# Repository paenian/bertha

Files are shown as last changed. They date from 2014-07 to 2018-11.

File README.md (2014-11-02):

bertha
======

Large format Rostock style printer, built with aluminum extrusions.

My plan is to design a large printer, emphasizing quality over cost.  Ideally there will be the 'full' version, and then various lower cost options.

The design of the plastic parts contained here is complete - that's not to say they won't be updated, just that everything in here is functional.

I am working on build instructions in a blog over here: http://berthareprap.blogspot.com/2013/05/mark-4-finally.html
I am currently constructing the very first machine, so instructions are coming out as I get build time.

Bill of Materials
===============
Frame BOM
-----
m3 x 8mm...........12&nbsp;&nbsp;&nbsp;&nbsp;Motor mounting<br>
m3 x 10mm..........12&nbsp;&nbsp;&nbsp;&nbsp;Bearing bar side mounts<br>
m3 x 16mm..........12&nbsp;&nbsp;&nbsp;&nbsp;Rod End clamps - use to hold rods in place temporarily, while glue sets up.<br>
m3 x 22mm..........12&nbsp;&nbsp;&nbsp;&nbsp;Rod End attachments - clamp the rod ends onto the bearing bar<br>
m3 x nuts..........24&nbsp;&nbsp;&nbsp;&nbsp;12 for the rod end clamp, 12 for bearing bar attachment<br>
m3 x locknut.......12&nbsp;&nbsp;&nbsp;&nbsp;rod end attachments<br>
<br>
m5 x 30mm..........15&nbsp;&nbsp;&nbsp;&nbsp;12 for V wheel mounts, 3 for idler mounts<br>
m5 x 10mm low p....72&nbsp;&nbsp;&nbsp;&nbsp;12 for each bracket<br>
m5 x nut...........12&nbsp;&nbsp;&nbsp;&nbsp;6 idler, 6 belt mount<br>
m5 x washer........6&nbsp;&nbsp;&nbsp;&nbsp;v-wheel clamping<br>
m5 x T-nut.........72&nbsp;&nbsp;&nbsp;&nbsp;12 for each bracket<br>
<br>
623 bearings.......36&nbsp;&nbsp;&nbsp;&nbsp;6 for each bearing bar.<br>
m3 x 2mm spacer....12&nbsp;&nbsp;&nbsp;&nbsp;http://www.mcmaster.com/#94669a210/=tgrbjv  4.5mm outside diameter.  6mm OD might be better, but they're significantly more expensive.<br>
8mm square carbon fiber rods....6&nbsp;&nbsp;&nbsp;&nbsp;Length forthcoming.  Gotta measure 'em.<br>
<br>
OpenBuilds Part Store bits
-----
1m v-rails.........3&nbsp;&nbsp;&nbsp;&nbsp;http://openbuildspartstore.com/black-v-slot-20-x-60mm/<br>
mini-V  wheel kit..12&nbsp;&nbsp;&nbsp;&nbsp;http://openbuildspartstore.com/mini-v-wheel-kit/<br>
idler kit..........3&nbsp;&nbsp;&nbsp;&nbsp;http://openbuildspartstore.com/smooth-idler-pulley-kit/<br>
Eccentric Spacers..6&nbsp;&nbsp;&nbsp;&nbsp;http://openbuildspartstore.com/eccentric-spacers/<br>
<br>
Misumi
-----
350mm 2060 extrusion, HFS5-2060-350.  This can be larger if you like, but you'll need to recalculate the triangles and rod lengths.<br>
<br>
Printed Bits
-----
Idler Bracket......6<br>
Idler Slider.......6<br>
Motor Bracket......6<br>
Hotend Effector....1&nbsp;&nbsp;&nbsp;&nbsp;These are in the new effectors directory!<br>
Rail Effector......3&nbsp;&nbsp;&nbsp;&nbsp;These are in the new effectors directory!<br>
Bearing Bar........6&nbsp;&nbsp;&nbsp;&nbsp;These are in the new effectors directory!<br>
Rod End...........12&nbsp;&nbsp;&nbsp;&nbsp;These are in the new effectors directory!<br>
<br>
<br>
<br>
<br>
Paul Chase.

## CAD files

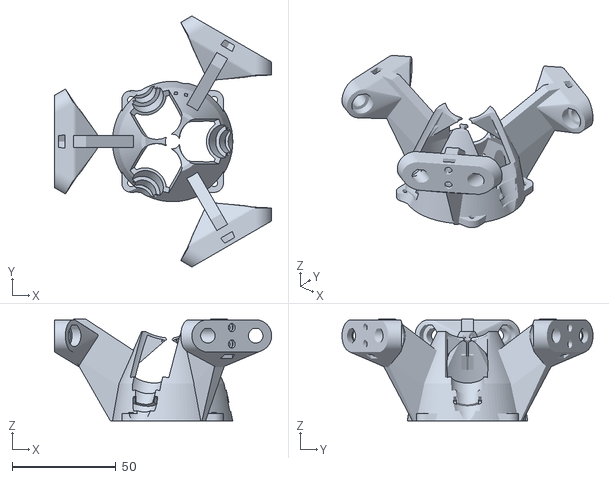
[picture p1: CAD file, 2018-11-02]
new_effectors/diamond_hotend_assembly_fixed.obj
104.7 x 120.9 x 49.0

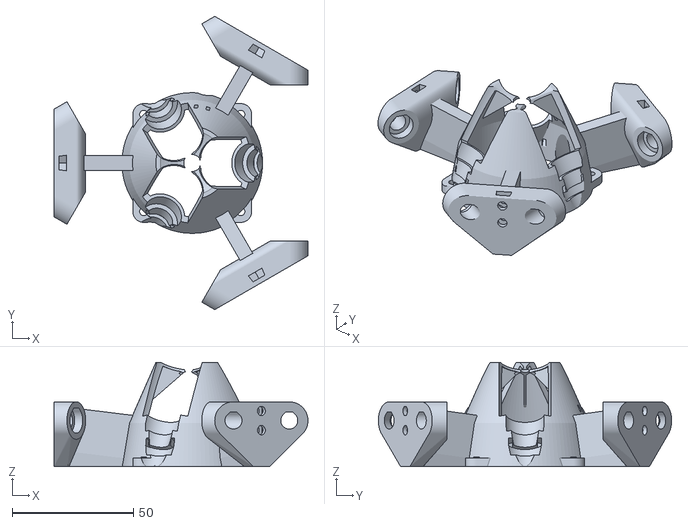
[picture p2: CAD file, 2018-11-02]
new_effectors/diamond_hotend_assembly.stl
104.7 x 120.9 x 43.0

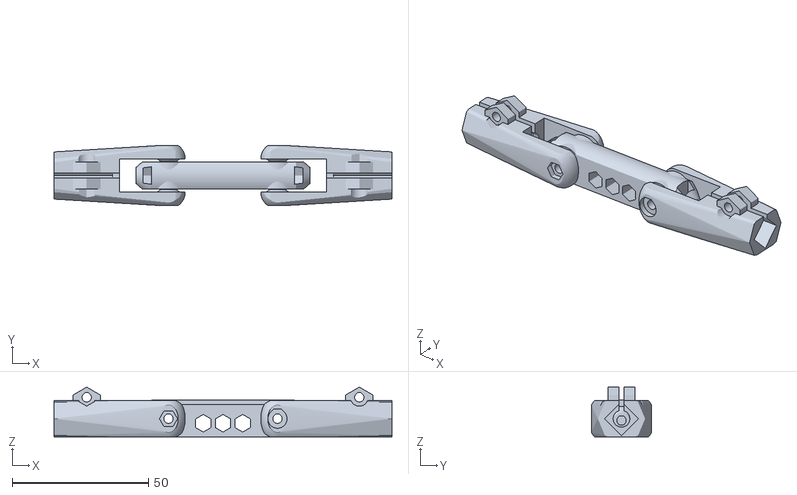
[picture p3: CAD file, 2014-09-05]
new_effectors/bearing_bar_assembly.stl
124.0 x 22.0 x 18.3

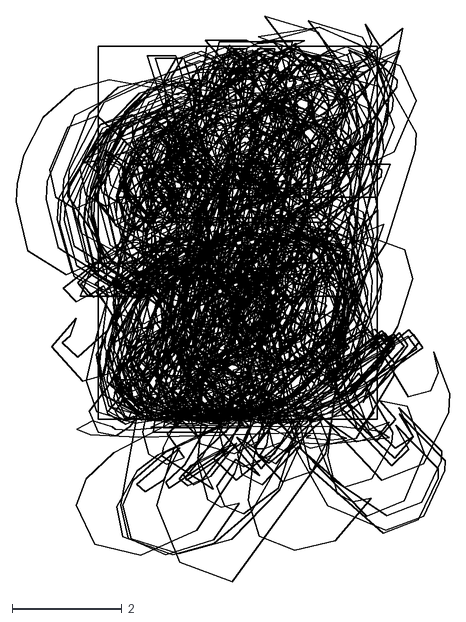
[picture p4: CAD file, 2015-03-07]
doors/Writescad/BlackRose.dxf
7.90 x 10.3

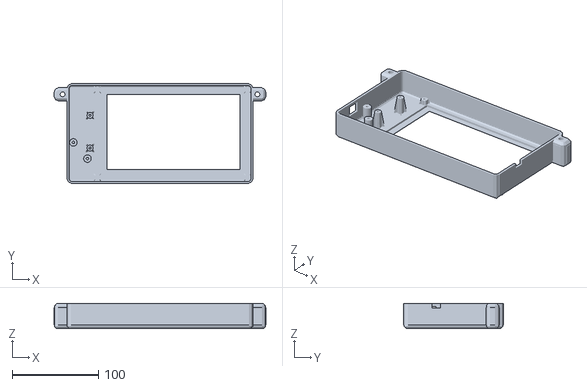
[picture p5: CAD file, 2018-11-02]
duet/PanelDueEnclosure.stl
246.4 x 115.8 x 29.1

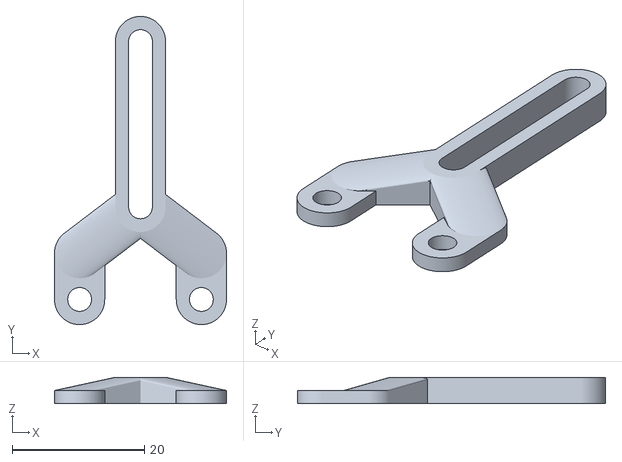
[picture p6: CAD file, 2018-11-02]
new_effectors/ir_sensor_mount.stl
26.0 x 46.6 x 4.00

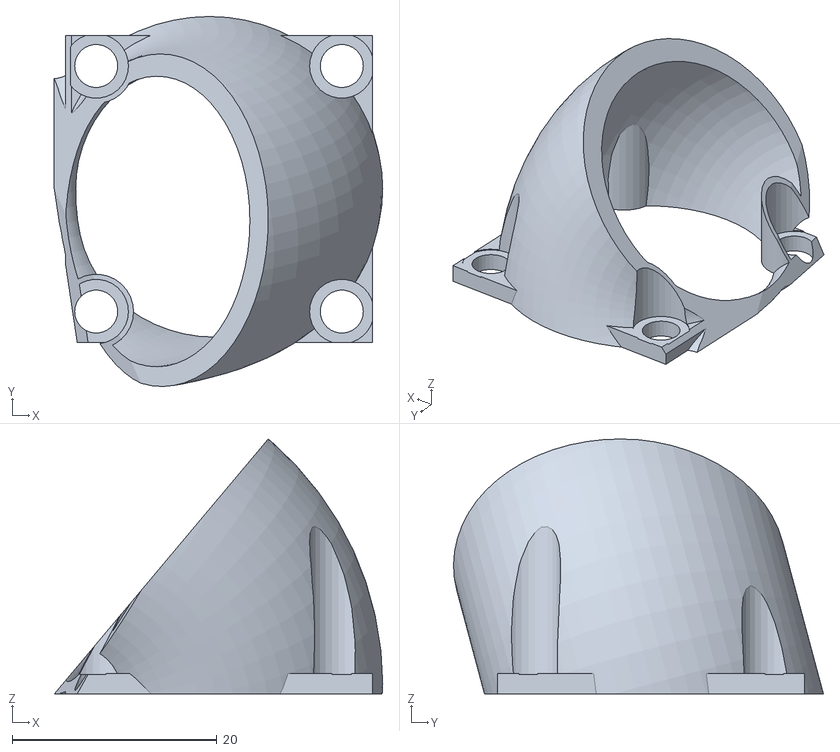
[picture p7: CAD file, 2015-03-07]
tinyduct.stl
32.1 x 36.2 x 24.9

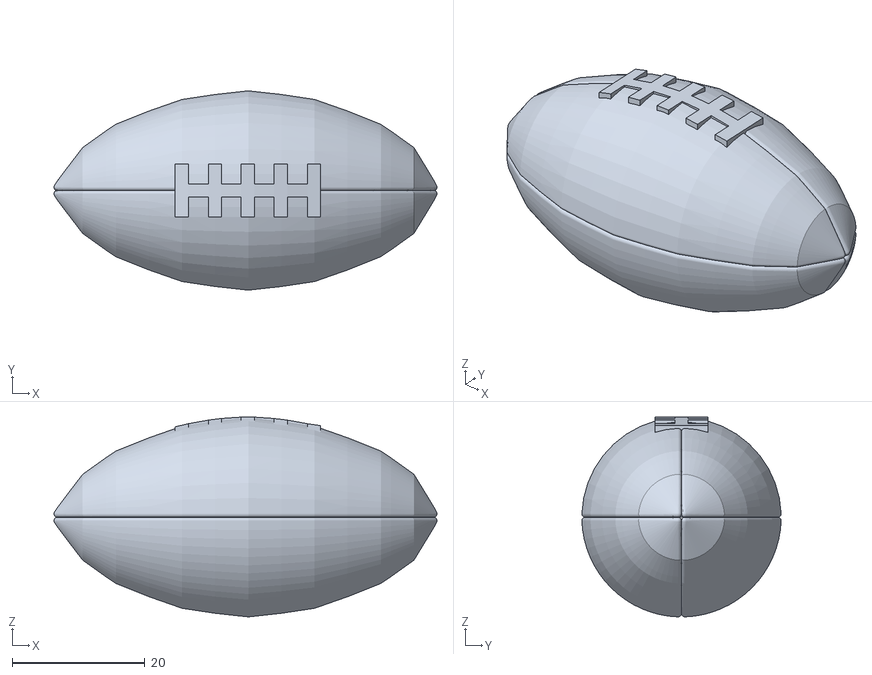
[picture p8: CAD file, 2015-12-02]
trophy/football.stl
57.8 x 30.1 x 30.2

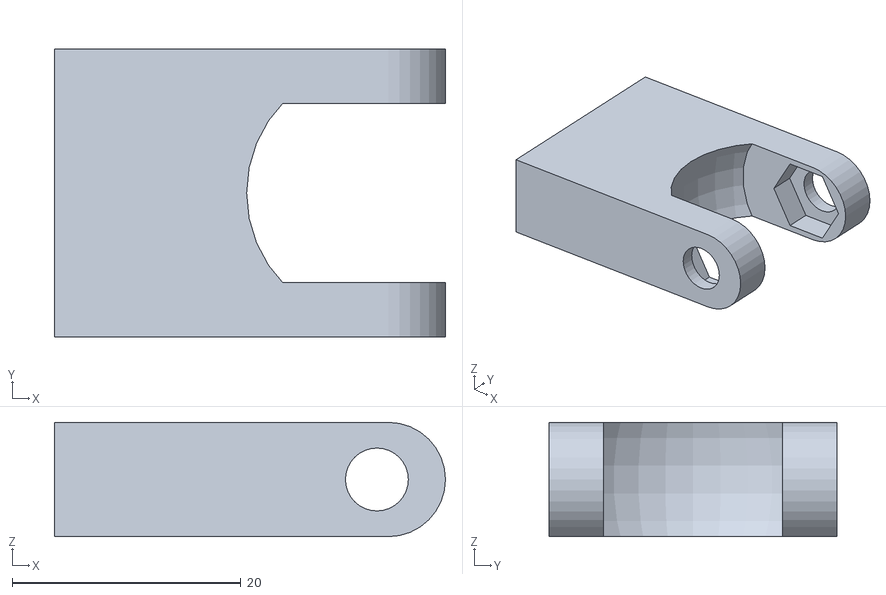
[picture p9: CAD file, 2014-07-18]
ujoints/rodend_inset.stl
34.2 x 25.2 x 10.0

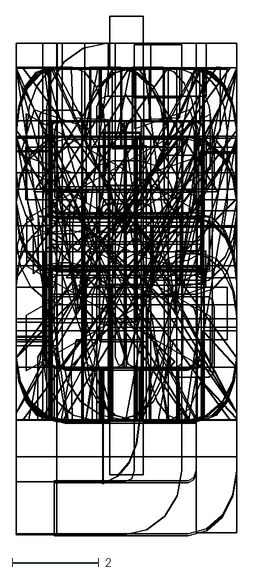
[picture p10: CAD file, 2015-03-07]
doors/Writescad/orbitron.dxf
5.08 x 12.0

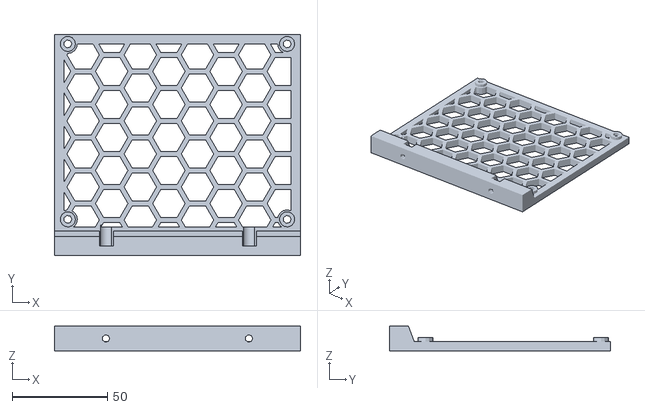
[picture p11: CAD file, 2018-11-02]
duet/duet_base.stl
129.0 x 116.0 x 13.0

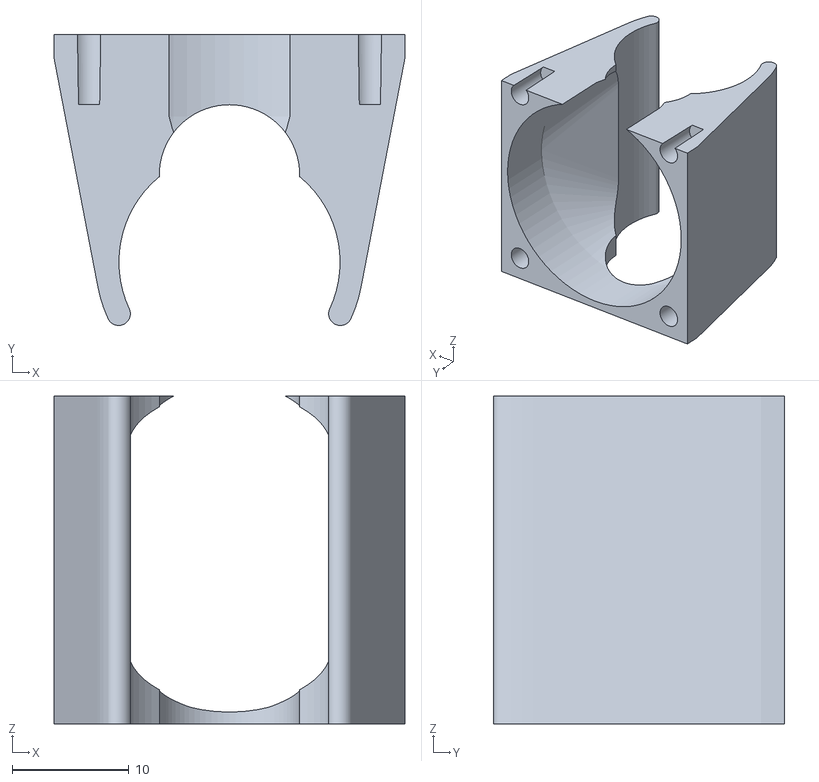
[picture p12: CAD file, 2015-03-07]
hexagon_fanshroud.stl
30.0 x 24.9 x 28.0

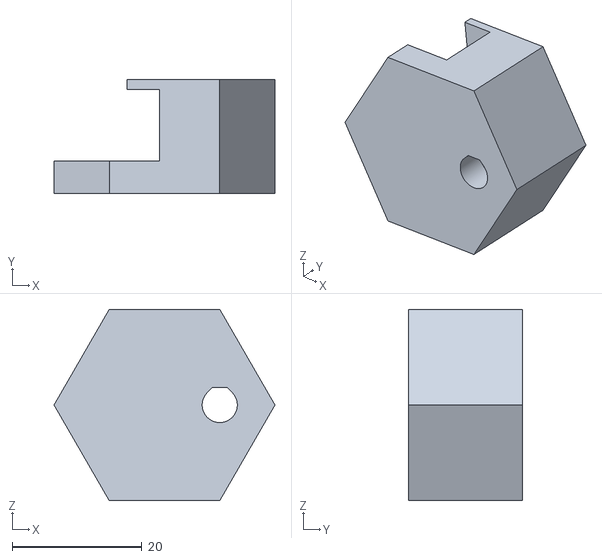
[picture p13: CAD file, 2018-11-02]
new_effectors/bed_clip.stl
34.0 x 17.5 x 29.4

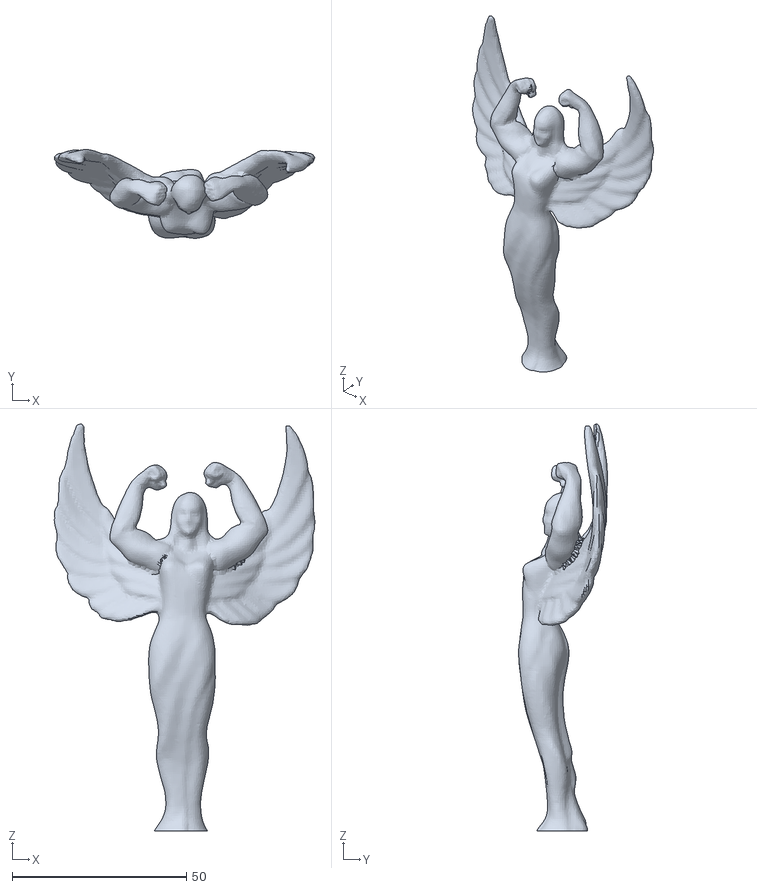
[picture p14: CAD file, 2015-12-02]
trophy/beefy_trophy.stl
74.8 x 25.5 x 116.9

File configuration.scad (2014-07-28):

$fn = 18;

slop = .2;

wall = 5;

bolt_slop = .5;
nut_slop = .85;
bolt_dia = 5+bolt_slop;
bolt_rad = bolt_dia/2;
bolt_cap_dia = 10+bolt_slop;
bolt_cap_rad = bolt_cap_dia/2;
nut_dia = 9+nut_slop;
nut_rad = nut_dia/2;
nut_height = 3.25;
lock_nut_height = 5.25;

m3bolt_dia = 3+bolt_slop;
m3bolt_rad = m3bolt_dia/2;
m3nut_dia = 6.1+nut_slop;
m3nut_rad = m3nut_dia/2;
m3nut_height = 3;

ext_x = 20+slop;
ext_y = 60+slop;

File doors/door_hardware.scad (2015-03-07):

use <write.scad>

base_rad = 30;
base_h = 20;
font_size = 10;

writecylinder("K N O X",[0,0,0],base_rad,base_h/2,h=font_size);

wall=5;

h1 = "BERTHA";

for(i=[0:len(h1)]) translate([0,0,i*font_size]) rotate([90,0,0]) scale([1.5,1,1]) write(h1[len(h1)-i],t=wall*3,h=font_size,center=true, font = "Writescad/orbitron.dxf");

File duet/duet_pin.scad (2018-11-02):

$fn = 36; 

module base() {

hull() {

 cylinder(h=3, d1=6, d2=8, center=false);
 
 
 
translate([0,0,40])
 
cylinder(h=3, d1=8, d2=6, center=false);
    
translate([3,-3,3])
 
cube ([1,6,43-3-3]);  
  
translate([3,-2,1])
  
cube ([1,4,41]);      
    
}

}


module holes() {

translate([-10,-5,3+8/2])
cube ([10,10,43-3-3-8]);   

cylinder(h=43, d=4, center=false);


translate([0,0,4.5])
cylinder(h = 43-3-3-8+5, d = 6.5, center = false, $fn = 6 );


}

difference (){
base();

holes();
    
}

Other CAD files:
ujoints/core.stl
doors/Writescad/knewave.dxf
e3dv6.stl
ujoints/bearing_arms.stl
new_effectors/configuration.scad
anglefan.scad
bearing_arms.scad
bed_clip.stl
bed_mount.scad
bed_mount.stl
brackets.scad
doors/Writescad/Letters.dxf
doors/Writescad/braille.dxf
doors/write.scad
duet/PanelDueEnclosure.scad
duet/duet_base.scad
e3dv6.scad
e3dv6_fan_mount.stl
effectors.scad
fan.stl
fan_mount.stl
foot.scad
foot.stl
foot_cabletie.stl
hotend_clamp.stl
hotend_effector.stl
hotend_fan_mount.stl
hotendeffector.scad
hotendeffector_fixed.stl
idler_bracket.stl
idler_guide.scad
idler_guide.stl
idler_slider.stl
joint.scad
joint_2.scad
lcd_mount.scad
lcd_mount.stl
lm8uu_clamp.scad
motor_bracket.stl
motor_fan.stl
new_effectors/bearing_bar.stl
new_effectors/bed_mounts.scad
new_effectors/bed_mounts.stl
new_effectors/diamond_hotend_assembly.scad
new_effectors/diamond_hotend_effector.stl
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

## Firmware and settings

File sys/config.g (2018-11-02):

; Think3DPrint3D configuration file for Mini Kossel for testing Duet WiFi

; Communication and general
M111 S0                             	; Debug off
M550 PMiniKosselWiFiTest		; Machine name and Netbios name (can be anything you like)
M551 Preprap                        	; Machine password (used for FTP)
;*** If you have more than one Duet on your network, they must all have different MAC addresses, so change the last digits
M540 P0xBE:0xEF:0xDE:0xAD:0xFE:0xED 	; MAC Address
;*** Wifi Networking
; M552 S1				; Enable WiFi. Disabled for setup and testing. Enable once set up on your network.

M555 P2                           	; Set output to look like Marlin
M575 P1 B57600 S1			; Comms parameters for PanelDue

G21                                 	; Work in millimetres
G90                                	; Send absolute coordinates...
M83                                 	; ...but relative extruder moves

; Axis and motor configuration
M569 P0 S1				; Drive 0 goes forwards
M569 P1 S1				; Drive 1 goes forwards
M569 P2 S1				; Drive 2 goes forwards
M569 P3 S1				; Drive 3 goes forwards
M569 P4 S1				; Drive 4 goes forwards
M574 X2 Y2 Z2 S1			; set endstop configuration (all endstops at high end, active high)
;*** The homed height is deliberately set too high in the following - you will adjust it during calibration
M665 R105.6 L215.0 B85 H250		; set delta radius, diagonal rod length, printable radius and homed height
M666 X0 Y0 Z0				; put your endstop adjustments here, or let auto calibration find them
M350 X16 Y16 E16 I1    			; Set 16x microstepping with interpolation
M92 X80 Y80 Z80				; Set axis steps/mm
M906 X1000 Y1000 Z1000 E800 I60		; Set motor currents (mA) and increase idle current to 60%
M201 X1000 Y1000 Z1000 E1000		; Accelerations (mm/s^2)
M203 X20000 Y20000 Z20000 E3600		; Maximum speeds (mm/min)
M566 X1200 Y1200 Z1200 E1200		; Maximum instant speed changes mm/minute

; Thermistors
M305 P0 T100000 B3950 R4700 H30 L0	; Put your own H and/or L values here to set the bed thermistor ADC correction
M305 P1 T100000 B3974 R4700 H30 L0	; Put your own H and/or L values here to set the first nozzle thermistor ADC correction
M305 P2 T100000 B3974 R4700 H30 L0	; Put your own H and/or L values here to set the second nozzle thermistor ADC correction
M570 S180				; Hot end may be a little slow to heat up so allow it 180 seconds

; Fans
M106 P1 H-1 				; disable thermostatic mode for fan 1

; Tool definitions
M563 P0 D0 H1                       	; Define tool 0
G10 P0 S0 R0                        	; Set tool 0 operating and standby temperatures
;*** If you have a single-nozzle build, comment the next 2 lines
M563 P1 D1 H2                      	; Define tool 1
G10 P1 S0 R0                       	; Set tool 1 operating and standby temperatures
M92 E663:663                       	; Set extruder steps per mm

; Z probe and compensation definition
;*** If you have a switch instead of an IR probe, change P1 to P4 in the following M558 command
M558 P1 X0 Y0 Z0			; Z probe is an IR probe and is not used for homing any axes
G31 X0 Y0 Z4.80 P500			; Set the zprobe height and threshold (put your own values here)

;*** If you are using axis compensation, put the figures in the following command
M556 S78 X0 Y0 Z0                   	; Axis compensation here

M208 S1 Z-0.2				; set minimum Z
;
T0					; select first hot end

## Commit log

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2013-03-28 Update brackets.scad
    Lower bracket is almost finished. Just adding some nice rounding etc.
    [brackets.scad]
2013-03-30 increased size slightly, in order to add a third screwhole to the side extrusion.
    [brackets.scad]
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2013-04-05 Top and bottom are complete. Untested as of yet. Hopefully the motor can be mounted on this version...
    [brackets.scad, idler.stl, idler_bracket.stl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]
2013-04-09 Starting on effectors.scad - this will contain both the hotend effector as well as the vertical column effectors.
    [brackets.scad, configuration.scad, effectors.scad]
2013-04-09 More work on the effector.
    All the components are in place, but I'm not sure how to join them together. I'd like to mount the single vwheel on some sort of tensioner, too - maybe rehash the idler tensioner?
    [effectors.scad]
2013-04-10 Finished rail effector version one.
    TODO: It needs a way to tension the single V-wheel.
    [configuration.scad, effectors.scad, rail_effector.stl]
2013-04-12 Added screw holes, updated rail effector
    rail effector still needs work. I want to make it tension-adjustable to
    grip the extrusion, but I'm not sure exactly how to do it without
    introducing slop.
    [brackets.scad, effectors.scad, idler.stl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]
2013-04-12 First complete rail effector
    not sure if I like the design, but it should be functional. Debating changing up the body, it looks too slim next to the beefy adjustable wheel slot.
    [effectors.scad]
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2013-04-19 Cleanup, minor updates to the effectors.
    Center effector mount has changed, but the clamps aren't done yet.
    [effectors.scad]
2013-04-22 More updates on the effector. It's ready to print, along with its hotend bracket to hold jheads. The measurements are not measurements - I just guessed, since I don't have any groovemounts to measure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
    [effectors.scad]
2013-04-23 minor changes, in support of fan. Mostly messing with it, but didn't get anything that worked well enough.
    [configuration.scad, effectors.scad]
2013-04-28 Designed the rod end, everything is ready for alpha build. Also re-rendered all STLs, and re-upped.
    [configuration.scad, effectors.scad, hotend_clamp.stl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]
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2013-04-28 Added a plate. You need three tower_plates.stl to make a printer, plus the hotend effector. I plan to color code my towers, because I think it'll look cool, and help me sort out which hotend's gone w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
    [tower_plate.scad, tower_plate.stl]
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2013-05-03 Make the Igus rod ends fit
    Updated the Igus connector blocks, and redesigned the hotend effector entirely. Effector now prints upside-down. Currently untested.
    [effectors.scad]
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2013-05-05 Widened the effectors, and updated their connections. Also increased slop, to make assembly easier.
    [configuration.scad, effectors.scad, hotend_effector.stl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]
2013-05-08 Redesigned the rod end
    Now it's tapered, so you can mount the carriages with the rod ends on top and it won't run into the carriage as much. Also prints horizontally, so it ought to be a lot stronger.
    [effectors.scad]
2013-05-08 Added a fan shroud.
    This will fit a 30mm fan on top of the hotend. There are no mounting holes for the fan, it can simply be hot glued in place.
    [effectors.scad]
2013-05-08 fix small hole at the base of the arms
    [effectors.scad]
2013-05-10 Minor updates, and updating all of the STLs. You still need three tower plates and a hotend effector :-)
    [brackets.scad, effectors.scad, hotend_clamp.stl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]
2013-05-11 Corrected the nut_rad - nuts should fit now.
    [configuration.scad, effectors.scad, rod_end.stl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]
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2013-05-13 Minor bugs shored up.
    [configuration.scad, effectors.scad, hotend_clamp.stl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]
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2013-05-16 Updated scads - re-oriented the idler slider for better printing, added in Doug's code to beef up the hotend clamp, secured the center of my hotend effector so that it'll be more likely to print prop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
    [brackets.scad, effectors.scad]
2013-05-16 Adding in the updated STLs. Also, the hotend effector had issues with not being manifold - not sure where, so I uploaded the netfabb cloud repaired version. Slic3r failed to slice the non-repaired on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
    [hotend_clamp.stl, hotend_effector.stl, hotendeffector_fixed.stl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]
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2013-05-27 Verifying STLs are correct.
    [hotend_effector.stl, hotendeffector_fixed.stl, tower_plate.scad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]
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2013-06-05 Added Doug's switch bracket, to hold the endstop within the idler bracket.
    [brackets.scad, switch_bracket.stl]
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2013-06-10 Created mounting brackets for the rumba, as well as a fan to cool it. Brackets as uploaded take m3 hardware - intended for 10mm m3 bolts used in conjunction with insertable t-nuts, which are also par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
    [brackets.scad, configuration.scad, fan_mount.stl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]
2013-06-13 Added some feet, mounts for the rumba and power supply. Right now I'm mounting the rumba within the bottom triangle, and the power supply within the top triangle. Not sure if that will continue, migh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
    I'm working on mountable extruders now.
    [foot.scad, foot.stl, power_mount.scad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]
2013-06-13 Initial STL of the extruder. Code is modified from Jonas's, as you can tell. It's somewhat hacked together. I'll clean up the code and post the .scad in a format compatible with my repo soon.
    The extruder is currently printing. If it works out I'll add the rest of the bits.
    [jonaskuehling_gregs-wade-v3 (repaired).stl, jonaskuehling_gregs-wade-v3.stl]
2013-06-15 Added more material to the base, and sized the pushfit hole properly.
    I'm not going to print this until my new pushfits come in, there's apparently a decent amount of variation.
    [jonaskuehling_gregs-wade-v3 (repaired).stl]
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2013-06-15 Not sure if I uploaded the right ones earlier. These are verified :-)
    [jonaskuehling_gregs-wade-v3 (repaired).stl, jonaskuehling_gregs-wade-v3.stl]
2013-06-15 Added the gears and idler for the extruder. Also modified the feet so I could route wires through the center of the aluminum extrusion.
    [biggearmod_fixed.stl, foot.scad, foot.stl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]
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2013-06-18 Added in a bed mount & clamp. Should fit on the rail someplace, printing now.
    The idea is to set the bed in and use a binder clip to hold it on. Minimum height here is about 6mm above the extrusion, it's sized for relatively short screws.
    [bed_clip.stl, bed_mount.scad, bed_mount.stl]
2013-06-18 Added a fan mount for the hotend. It's for a 40mm fan - I think there'll be enough room to route the hotend bowden tubes away from the fan. Will print soon.
    Paul
    [effectors.scad, hotend_fan_mount.stl]
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2013-06-24 Minor fixes to the power mount - the back wall was too thick due to bad coding.
    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
    [power_mount.scad, power_mount.stl, power_switch_mount.stl]
2013-07-09 First commit of brand-new rail effector. Uses washers to stand off the V-wheels, and no longer needs a wheel slider, it's all one piece. Only issue is if it twists on tightening - recommend printing 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
    [effectors.scad, rail_effector.stl]
2013-07-10 Realized I could shrink the part a bit without losing any rigidity... so I did. Still initial commit, it'll be printing soon.
    [effectors.scad, rail_effector.stl]
2013-07-10 Stupid mistake on the last STL. Fixed so that the synchromesh guides go all the way through, also beefed up the ends a bit.
    [effectors.scad, rail_effector.stl]
2013-08-06 Updated brackets to allow T-nuts to be post-inserted into the slots. They will be updated again soon, to add switch mounts and to let the idler be mounted upside down.
    [idler_bracket.stl, motor_bracket.stl]
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2013-08-06 Added endstop mount to motor bracket, fixed idler mount to support push mounting.
    [brackets.scad, idler_bracket.stl, idler_slider.stl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]
2013-08-17 Added a simple bracket mount for the RRD LCD, plus a little tslot guide to snap wires in.
    [lcd_mount.scad, lcd_mount.stl, slot_snap.scad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]
2013-08-18 Added a fan that can slide onto the back of a motor, ala Doug's design.
    [motor_fan.stl, rumba_mount.scad]
2013-08-20 Fixed the idler bracket - it now has about 5mm more travel.
    [brackets.scad]
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2013-08-21 Last tower plate was using the pull-style idlers, this has the modern, push idlers. Assumes that your motors live at the top, with the endstops. With a push idler, you can adjust belt tension without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
    [tower_plate.scad, tower_plate.stl]
2013-08-21 New design for the hotend effector.
    Should be more rigid, and I'm thinking about trying out different attachments for the rods - this gives me more flexibility there.
    [effectors.scad]
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2013-09-11 Shortened the hotend effector & modified its angles for better clearance using u-joint rod ends.
    [configuration.scad, effectors.scad, hotend_effector.stl]
2013-09-11 Initial commit of bearing arms. These are universal joints to replace the existing rod ends and igus rod end bearings.
    [bearing_arms.scad, triple.stl, triple_arms.stl]
2013-09-11 Should be the first usable commit of arms with three bearings in each end. Proper universal joints, with enough movement on either side to shorten the arms considerably. They are printing now.
    [bearing_arms.scad, triple.stl, triple_arms.stl]
2013-09-12 Changed the rod end effectors to support better adjustment using female rod ends. Also lets you put springs in, to prevent minor head crashes :-)
    [effectors.scad]
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2013-09-17 Finished new rod ends. They're slightly beefier, and allow infinite fine adjustment of rod length. The length of the carbon fiber should now be 245mm. The rod end bearings are metal, with a 5mm male 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
    [effectors.scad, hotend_effector.stl, rod_end.stl]
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2013-10-06 Reduced the arm radius from 40 to 34, and redesigned the fillets for more strength. To use it, you need to change the END_EFFECTOR_HORIZONTAL_OFFSET to 34. This is as small as it can go without chang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
    [effectors.scad, hotend_effector.stl]
2013-10-23 Cleaning effector file
    Deleted old code (will upload later), made more things into variables, fixed some parametric errors. This is in preparation of major renovations - I plan to modify the hotends to be centralized, with each having their own fan. That'll allow me to reduce the arm separation, which should help with the effector's rigidity.
    [effectors.scad]
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2014-02-01 Fixed the rod ends - they were below the printbed on the last upload.
    [effectors.scad, tower_plate.scad, tower_plate.stl]
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2014-08-17 Newest bearing bars and effectors. Not sure how functional the hotend effector is, issue is the tops of the extruders. Planning to use e3d v6 extruders, which should work, but I don't have any in han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
    [bearing_bar.stl, bearing_bar_assembly.stl, configuration.scad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]
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2014-09-27 Changed many of the parts to m5 hardware, since the new brackets let you slip T-nuts in easily. Added bed_mounts - to mount pressure sensors and to hold the bed in place.
    [bed_mounts.scad, bed_mounts.stl, configuration.scad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]
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
